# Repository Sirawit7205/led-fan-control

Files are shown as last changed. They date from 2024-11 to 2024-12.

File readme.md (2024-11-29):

# LED Fan Controller

This is an open-source KiCAD design files for a retrofitting controller for cheap rechargeable USB fan with LED lights.

This board is an upgrade (I hope) for the old control board for lead-acid battery that broke down.

## Pictures

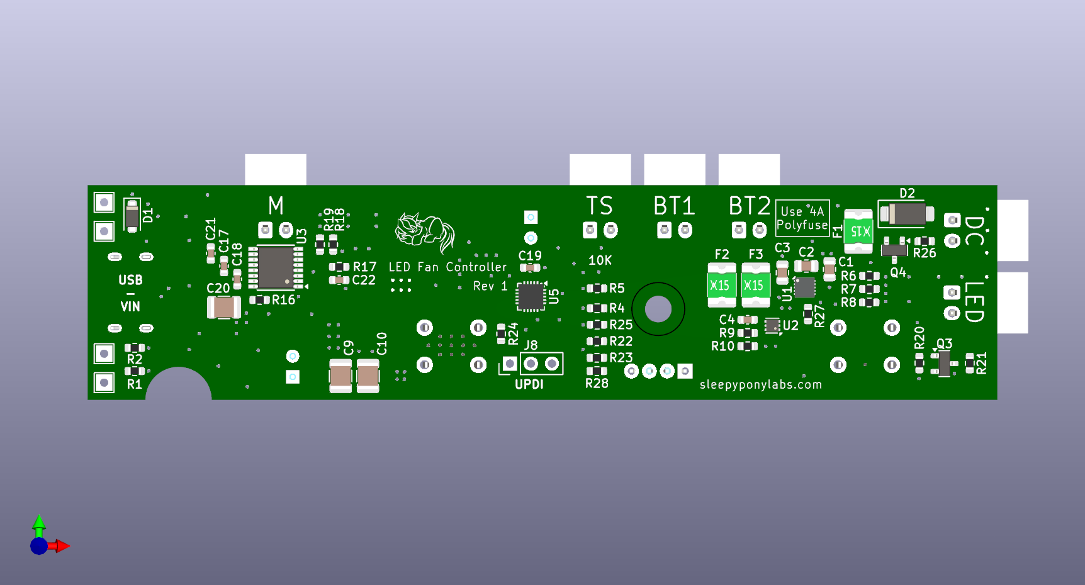
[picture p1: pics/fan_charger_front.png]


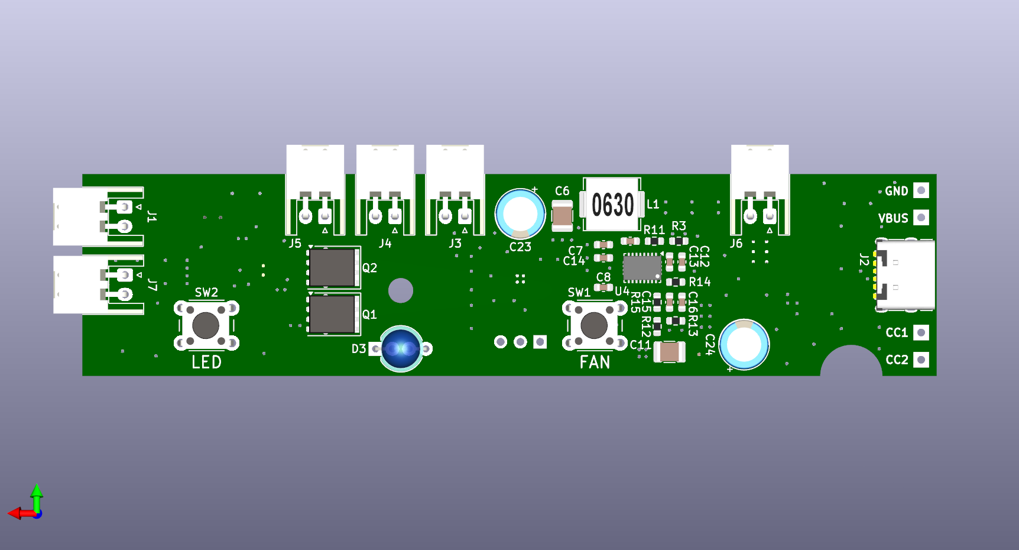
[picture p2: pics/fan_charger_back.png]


## Features

- 1A Charging via USB Type-C port or external 5V power.
- BQ25185DLH Battery charger IC
- BQ29701DSE Battery protection IC with extremely low RDS(on) MOSFET pair
- TPS61088RHL Boost converter from Vbat to 8V motor voltage
- DRV8876PWP Brushed DC Fan driver
- MCU control for fan and led levels.
	
## Revisions

We are currently at Revision 1. Changelog is below:

**Revision 1 (July 2024)**
 - Initial Design
 - Does work, but the Power Path feature on BQ25185DLH is not suitable for high current without cooling. Hits thermal limit in a few minutes.
 - Need to switch to another conventional 1A charger IC.
 - May need to remove DC jack connector as the existing board in the fan is not that good at handling the current.

## What is provided

**The schematics, PCB design, and an interactive BOM is provided.**

Hardware is licensed under `SPDX-License-Identifier: CERN-OHL-S-2.0`

Software is licensed under `SPDX-License-Identifier: GPL` (Firmware is WIP and will be uploaded later.)

Documentation is licensed under `SPDX-License-Identifier: CC-BY-SA-4.0`

## Ordering

You can export gerbers from this project and order the board yourself. You can also use the link below to directly order from Aisler.
https://aisler.net/p/YHUKIBMT

## Credits

 - AMPLF0630 inductor model by Aleksey Zablotskiy: https://grabcad.com/library/amplf-mpc-aspi-etc-smd-power-inductors-1
 - miniSMDC150F fuse model by Karol Novak: https://grabcad.com/library/minismdc150f-1
 - QFN packages model by Jason Traud: https://grabcad.com/library/qfn-packages-1
 - WSON-10 package model by Alex SAR: https://grabcad.com/library/sda10a-rev-a-wson-10-1
 - USB Type-C 6-pin SMD model by ni_ni: https://grabcad.com/library/usb-type-c-smd-6pin-1
 - VQFN-20 package model by Cristian Deenen: https://grabcad.com/library/vqfn-20-3x3mm-1

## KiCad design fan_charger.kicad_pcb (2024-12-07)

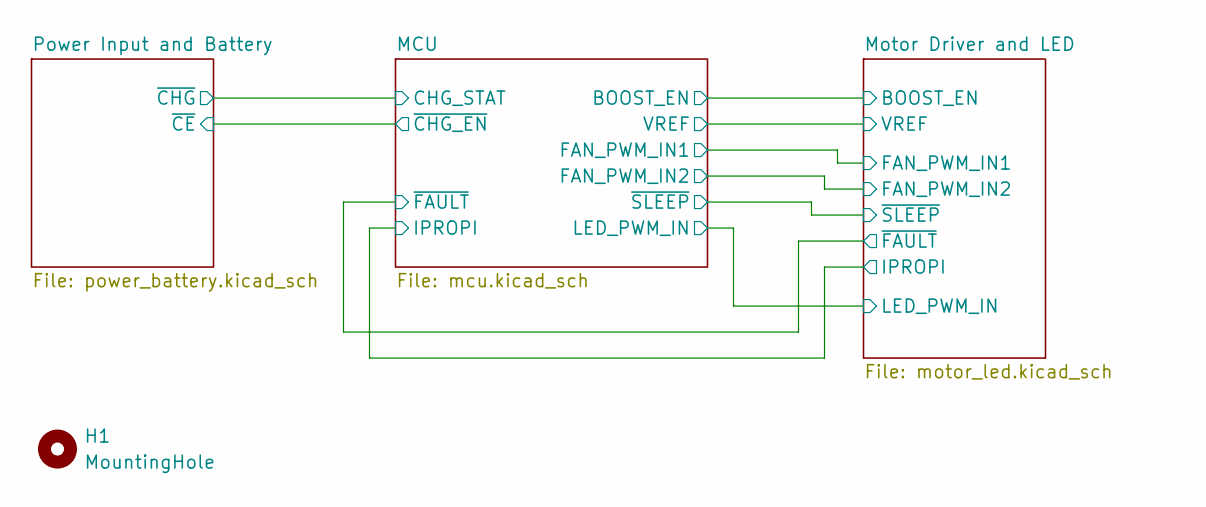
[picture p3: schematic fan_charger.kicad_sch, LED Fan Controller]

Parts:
H1: MountingHole; MountingHole_3.2mm_M3

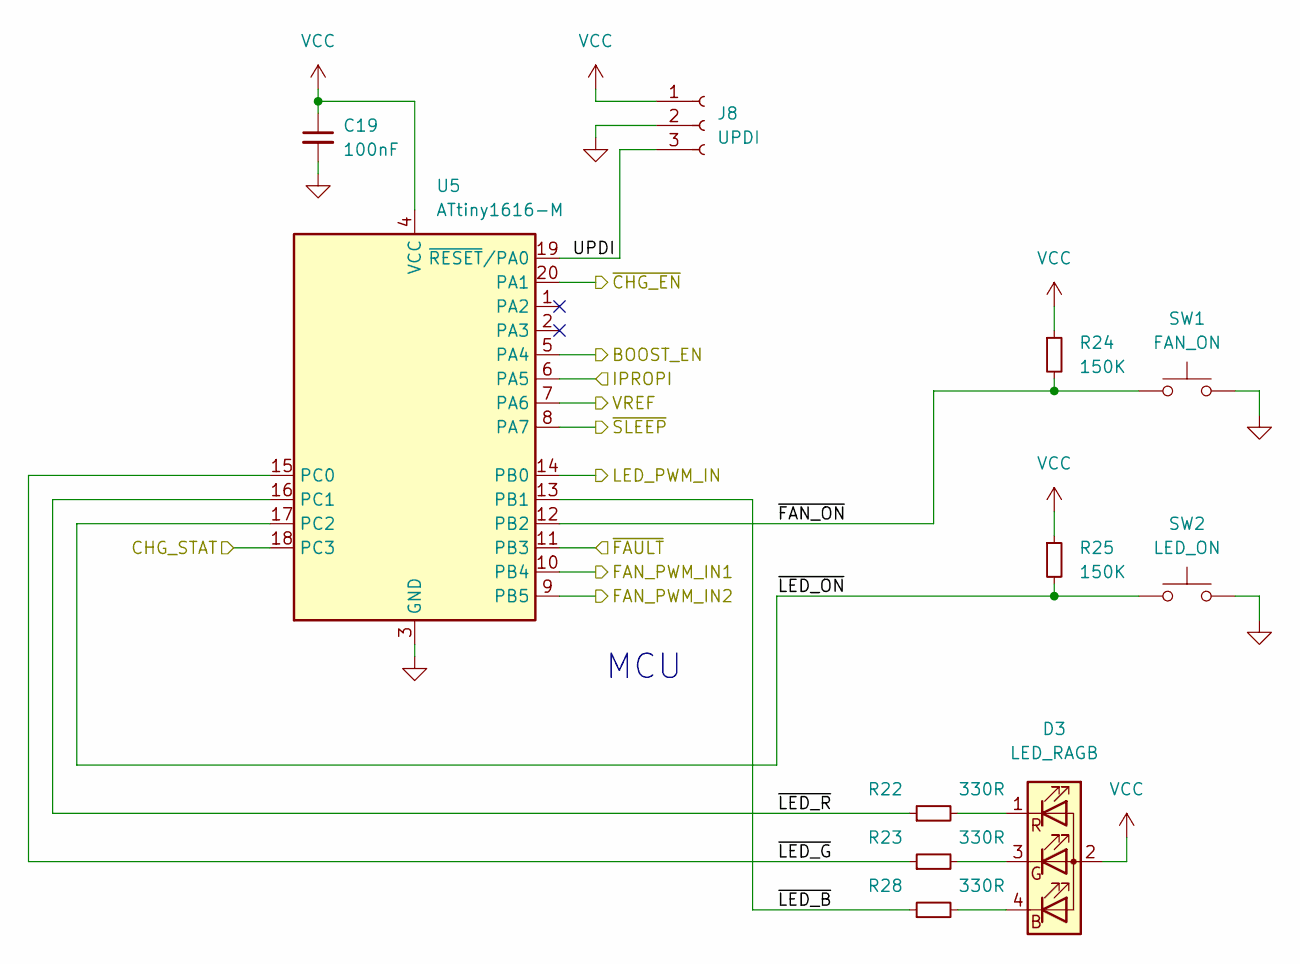
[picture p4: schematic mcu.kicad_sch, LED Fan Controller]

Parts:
C19: 100nF; C_0603_1608Metric
D3: LED_RAGB; LED_D5.0mm-4_RGB_Wide_Pins
J8: UPDI; PinHeader_1x03_P2.54mm_Vertical
R22, R23, R28: 330R; R_0603_1608Metric
R24, R25: 150K; R_0603_1608Metric
SW1: FAN_ON; SW_PUSH_6mm
SW2: LED_ON; SW_PUSH_6mm
U5: ATtiny1616-M; VQFN-20-1EP_3x3mm_P0.4mm_EP1.7x1.7mm

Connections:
/MCU/BOOST_EN: U5.5 (PA4); also elsewhere on the board
/MCU/CHG_STAT: U5.18 (PC3); also elsewhere on the board
/MCU/FAN_PWM_IN1: U5.10 (PB4); also elsewhere on the board
/MCU/FAN_PWM_IN2: U5.9 (PB5); also elsewhere on the board
/MCU/IPROPI: U5.6 (PA5); also elsewhere on the board
/MCU/LED_PWM_IN: U5.14 (PB0); also elsewhere on the board
/MCU/UPDI: J8.3, U5.19 (~RESET/PA0)
/MCU/VREF: U5.7 (PA6); also elsewhere on the board
/MCU/~CHG_EN: U5.20 (PA1); also elsewhere on the board
/MCU/~FAN_ON: R24.2, SW1.1, U5.12 (PB2)
/MCU/~FAULT: U5.11 (PB3); also elsewhere on the board
/MCU/~LED_B: R28.1, U5.13 (PB1)
/MCU/~LED_G: R23.1, U5.15 (PC0)
/MCU/~LED_ON: R25.2, SW2.1, U5.17 (PC2)
/MCU/~LED_R: R22.1, U5.16 (PC1)
/MCU/~SLEEP: U5.8 (PA7); also elsewhere on the board
GND: C19.2, J8.2, SW1.2, SW2.2, U5.3 (GND), U5.21 (GND); also elsewhere on the board
unnamed: D3.4 (BK), R28.2
unnamed: D3.3 (GK), R23.2
unnamed: D3.1 (RK), R22.2
VCC: C19.1, D3.2 (A), J8.1, R24.1, R25.1, U5.4 (VCC); also elsewhere on the board

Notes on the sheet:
MCU

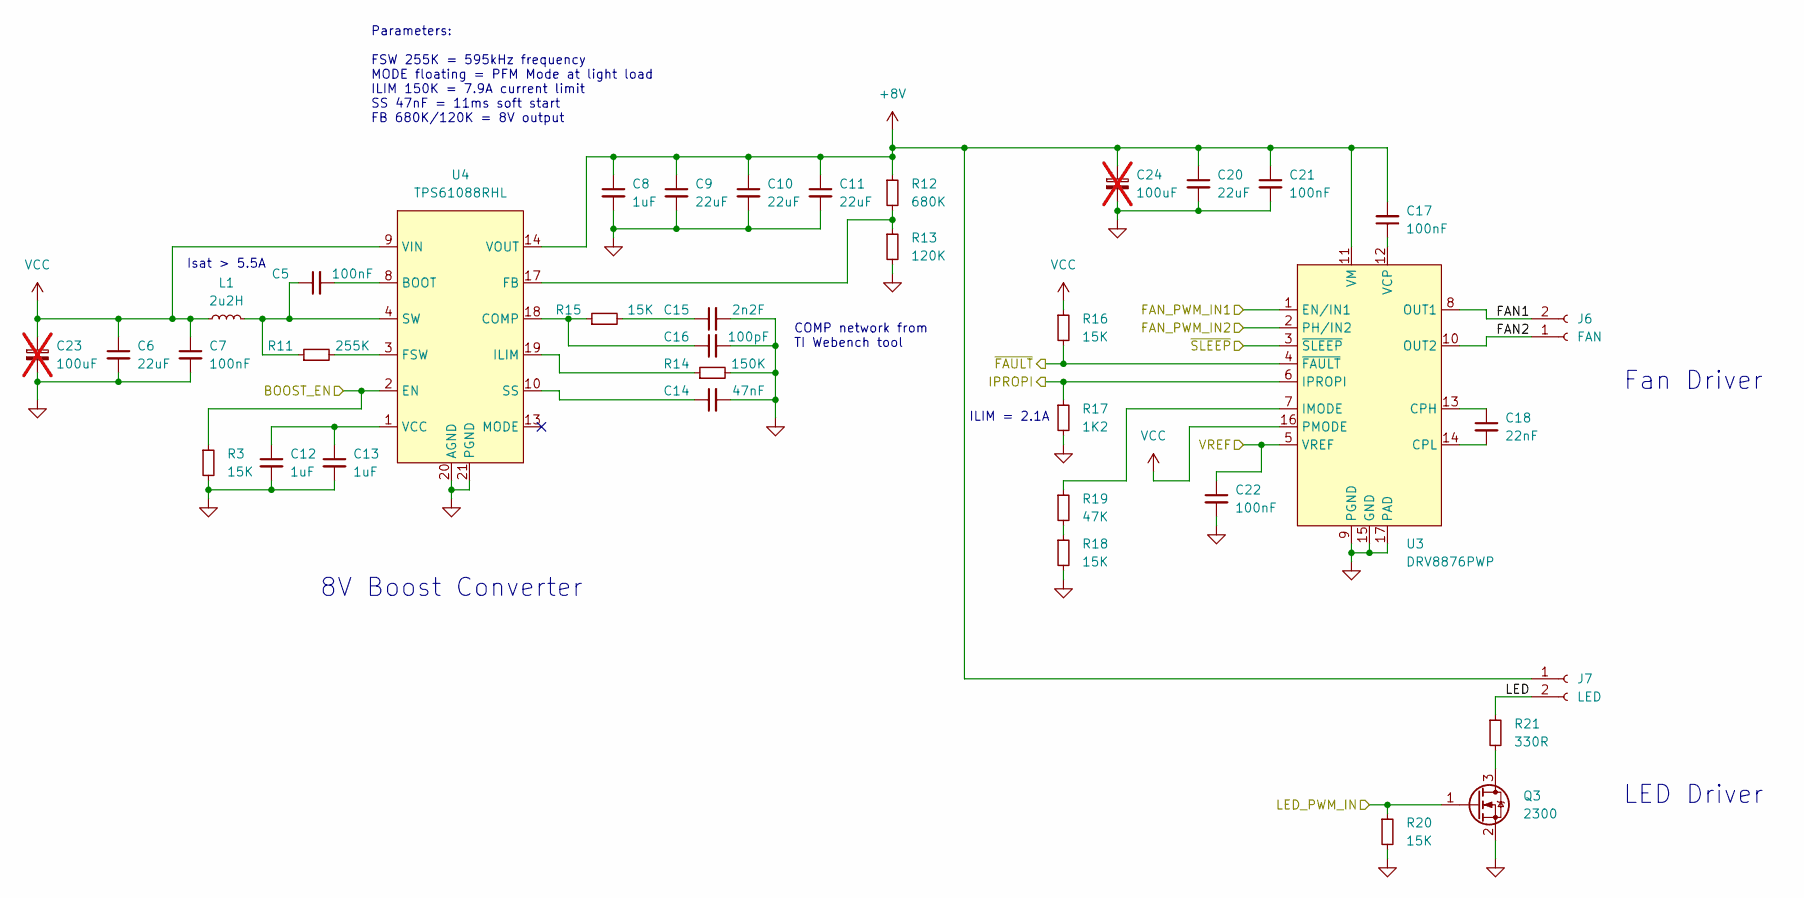
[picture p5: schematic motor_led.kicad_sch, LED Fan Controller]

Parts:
C5, C7, C17, C21, C22: 100nF; C_0603_1608Metric
C6, C9, C10, C11, C20: 22uF; C_1210_3225Metric
C8, C12, C13: 1uF; C_0603_1608Metric
C14: 47nF; C_0603_1608Metric
C15: 2n2F; C_0603_1608Metric
C16: 100pF; C_0603_1608Metric
C18: 22nF; C_0603_1608Metric
C23, C24: 100uF; CP_Radial_D6.3mm_P2.50mm; not fitted
J6: FAN; JST_XH_S2B-XH-A_1x02_P2.50mm_Horizontal
J7: LED; JST_XH_S2B-XH-A_1x02_P2.50mm_Horizontal
L1: 2u2H; L_Abracon_ASPI-0630LR
Q3: 2300; SOT-23
R3, R15, R16, R18, R20: 15K; R_0603_1608Metric
R11: 255K; R_0603_1608Metric
R12: 680K; R_0603_1608Metric
R13: 120K; R_0603_1608Metric
R14: 150K; R_0603_1608Metric
R17: 1K2; R_0603_1608Metric
R19: 47K; R_0603_1608Metric
R21: 330R; R_0603_1608Metric
U3: DRV8876PWP; TSSOP-16-1EP_4.4x5mm_P0.65mm
U4: TPS61088RHL; Texas_VQFN-RHL-20

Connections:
+8V: C8.1, C9.1, C10.1, C11.1, C17.2, C20.1, C21.1, C24.1, J7.1, R12.1, U3.11 (VM), U4.14 (VOUT), U4.15 (VOUT), U4.16 (VOUT)
/MCU/BOOST_EN: R3.1, U4.2 (EN); also elsewhere on the board
/MCU/FAN_PWM_IN1: U3.1 (EN/IN1); also elsewhere on the board
/MCU/FAN_PWM_IN2: U3.2 (PH/IN2); also elsewhere on the board
/MCU/IPROPI: R17.1, U3.6 (IPROPI); also elsewhere on the board
/MCU/LED_PWM_IN: Q3.1 (G), R20.1; also elsewhere on the board
/MCU/VREF: C22.1, U3.5 (VREF); also elsewhere on the board
/MCU/~FAULT: R16.2, U3.4 (~FAULT); also elsewhere on the board
/MCU/~SLEEP: U3.3 (~SLEEP); also elsewhere on the board
/Motor Driver and LED/FAN1: J6.2, U3.8 (OUT1)
/Motor Driver and LED/FAN2: J6.1, U3.10 (OUT2)
/Motor Driver and LED/LED: J7.2, R21.1
GND: C6.2, C7.2, C8.2, C9.2, C10.2, C11.2, C12.2, C13.2, C14.2, C15.2, C16.2, C20.2, C21.2, C22.2, C23.2, C24.2, Q3.2 (S), R3.2, R13.2, R14.2, R17.2, R18.2, R20.2, U3.9 (PGND), U3.15 (GND), U3.17 (PAD), U4.20 (AGND), U4.21 (PGND); also elsewhere on the board
unnamed: C5.1, L1.2, R11.1, U4.4 (SW), U4.5 (SW), U4.6 (SW), U4.7 (SW)
unnamed: C15.1, R15.2
unnamed: Q3.3 (D), R21.2
unnamed: R18.1, R19.2
unnamed: C18.1, U3.13 (CPH)
unnamed: C18.2, U3.14 (CPL)
unnamed: R19.1, U3.7 (IMODE)
unnamed: C17.1, U3.12 (VCP)
unnamed: C5.2, U4.8 (BOOT)
unnamed: C16.1, R15.1, U4.18 (COMP)
unnamed: R12.2, R13.1, U4.17 (FB)
unnamed: R11.2, U4.3 (FSW)
unnamed: R14.1, U4.19 (ILIM)
unnamed: C14.1, U4.10 (SS)
unnamed: C12.1, C13.1, U4.1 (VCC)
VCC: C6.1, C7.1, C23.1, L1.1, R16.1, U3.16 (PMODE), U4.9 (VIN); also elsewhere on the board

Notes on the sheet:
Fan Driver
Isat > 5.5A
LED Driver
Parameters: FSW 255K = 595kHz frequency MODE floating = PFM Mode at light load ILIM 150K = 7.9A current limit SS 47nF = 11ms soft start FB 680K/120K = 8V output
ILIM = 2.1A
8V Boost Converter
COMP network from TI Webench tool

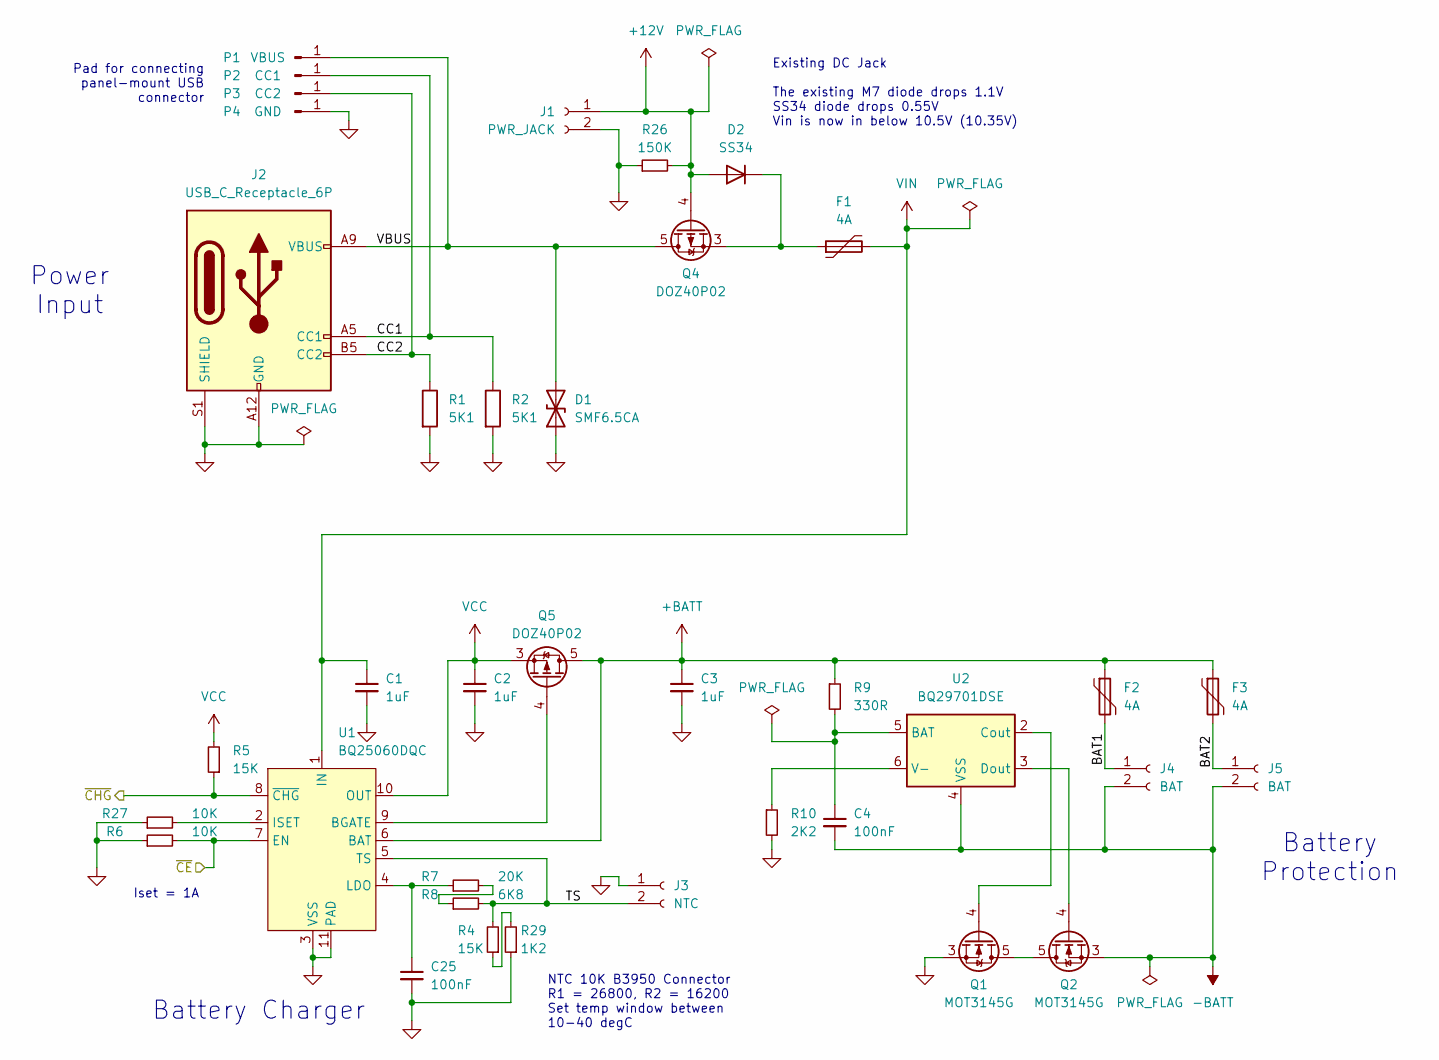
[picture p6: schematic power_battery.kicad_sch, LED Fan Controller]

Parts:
C1, C2, C3: 1uF; C_0805_2012Metric
C4, C25: 100nF; C_0603_1608Metric
D1: SMF6.5CA; D_SOD-123F
D2: SS34; D_SMA
F1, F2, F3: 4A; Fuse_1812_4532Metric
J1: PWR_JACK; JST_XH_S2B-XH-A_1x02_P2.50mm_Horizontal
J2: USB_C_Receptacle_6P; USB_C_Receptacle_HRO_TYPE-C-31-M-17
J3: NTC; JST_XH_S2B-XH-A_1x02_P2.50mm_Horizontal
J4, J5: BAT; JST_XH_S2B-XH-A_1x02_P2.50mm_Horizontal
P1: VBUS; TestPoint_THTPad_2.0x2.0mm_Drill1.0mm
P2: CC1; TestPoint_THTPad_2.0x2.0mm_Drill1.0mm
P3: CC2; TestPoint_THTPad_2.0x2.0mm_Drill1.0mm
P4: GND; TestPoint_THTPad_2.0x2.0mm_Drill1.0mm
Q1, Q2: MOT3145G; PQFN-8-EP_6x5mm_P1.27mm_Generic
Q4, Q5: DOZ40P02; VSON-8_3.3x3.3mm_P0.65mm_NexFET
R1, R2: 5K1; R_0603_1608Metric
R4, R5: 15K; R_0603_1608Metric
R6, R27: 10K; R_0603_1608Metric
R7: 20K; R_0603_1608Metric
R8: 6K8; R_0603_1608Metric
R9: 330R; R_0603_1608Metric
R10: 2K2; R_0603_1608Metric
R26: 150K; R_0603_1608Metric
R29: 1K2; R_0603_1608Metric
U1: BQ25060DQC; WSON-10-1EP_2x3mm_P0.5mm_EP0.84x2.4mm
U2: BQ29701DSE; WSON-6_1.5x1.5mm_P0.5mm

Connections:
+12V: D2.2 (A), J1.1, Q4.4 (G), R26.2
+BATT: C3.1, F2.1, F3.1, Q5.5 (D), R9.1, U1.6 (BAT)
-BATT: C4.2, J4.2, J5.2, Q2.1 (S), Q2.2 (S), Q2.3 (S), U2.4 (VSS)
/MCU/CHG_STAT: R5.1, U1.8 (~CHG); also elsewhere on the board
/MCU/~CHG_EN: R6.2, U1.7 (EN); also elsewhere on the board
/Power Input and Battery/BAT1: F2.2, J4.1
/Power Input and Battery/BAT2: F3.2, J5.1
/Power Input and Battery/CC1: J2.A5 (CC1), P2.1, R2.1
/Power Input and Battery/CC2: J2.B5 (CC2), P3.1, R1.1
/Power Input and Battery/TS: J3.2, R4.2, R8.2, U1.5 (TS)
/Power Input and Battery/VBUS: D1.2 (A2), J2.A9 (VBUS), J2.B9 (VBUS), P1.1, Q4.5 (D)
GND: C1.2, C2.2, C3.2, C25.2, D1.1 (A1), J1.2, J2.A12 (GND), J2.B12 (GND), J2.S1 (SHIELD), J3.1, P4.1, Q1.1 (S), Q1.2 (S), Q1.3 (S), R1.2, R2.2, R6.1, R10.2, R26.1, R27.1, R29.1, U1.3 (VSS), U1.11 (PAD); also elsewhere on the board
unnamed: D2.1 (K), F1.1, Q4.1 (S), Q4.2 (S), Q4.3 (S)
unnamed: Q1.5 (D), Q2.5 (D)
unnamed: Q1.4 (G), U2.2 (Cout)
unnamed: Q2.4 (G), U2.3 (Dout)
unnamed: Q5.4 (G), U1.9 (BGATE)
unnamed: R7.2, R8.1
unnamed: R4.1, R29.2
unnamed: R27.2, U1.2 (ISET)
unnamed: C25.1, R7.1, U1.4 (LDO)
unnamed: C4.1, R9.2, U2.5 (BAT)
unnamed: R10.1, U2.6 (V-)
VCC: C2.1, Q5.1 (S), Q5.2 (S), Q5.3 (S), R5.2, U1.10 (OUT); also elsewhere on the board
VIN: C1.1, F1.2, U1.1 (IN)

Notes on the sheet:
Existing DC Jack The existing M7 diode drops 1.1V SS34 diode drops 0.55V Vin is now in below 10.5V (10.35V)
Battery Charger
NTC 10K B3950 Connector R1 = 26800, R2 = 16200 Set temp window between 10-40 degC
Battery Protection
Power Input
Pad for connecting panel-mount USB connector
Iset = 1A

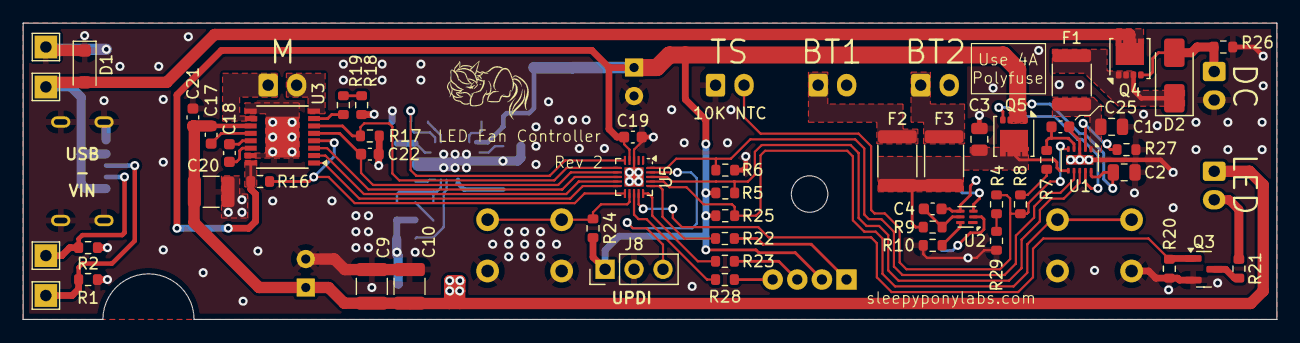
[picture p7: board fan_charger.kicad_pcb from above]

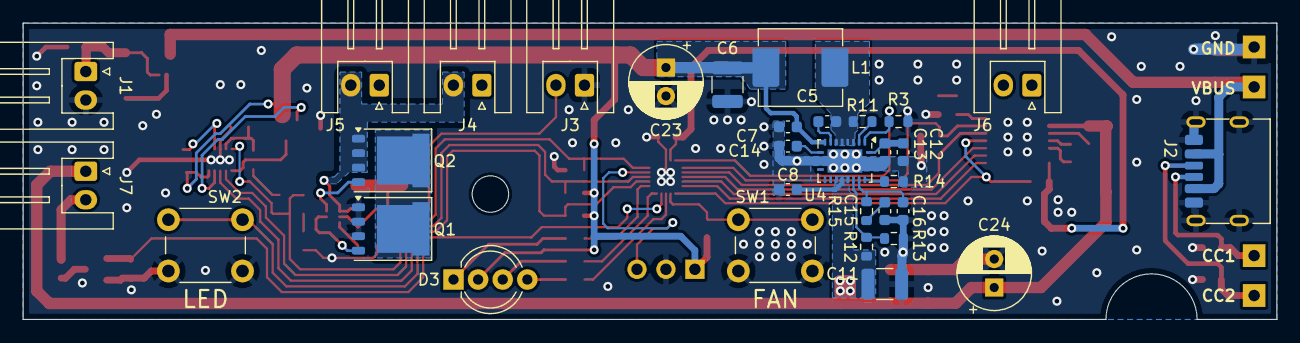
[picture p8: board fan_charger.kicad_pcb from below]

Board: 2 copper layers, 110.0 x 26.0 mm, 86 parts (32 on the bottom side), 61 nets.
